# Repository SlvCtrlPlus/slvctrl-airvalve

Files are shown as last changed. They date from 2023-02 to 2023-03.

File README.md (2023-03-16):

# slvctrl-airvalve

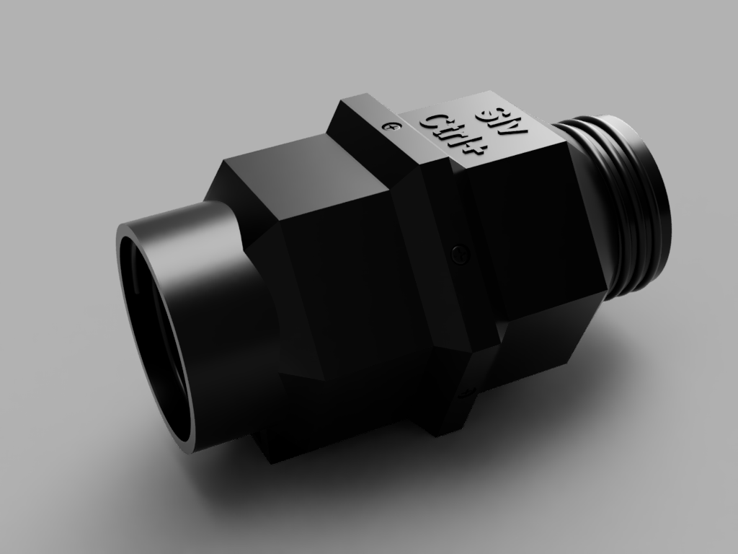
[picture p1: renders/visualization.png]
Air Valve Visualization


## Schema
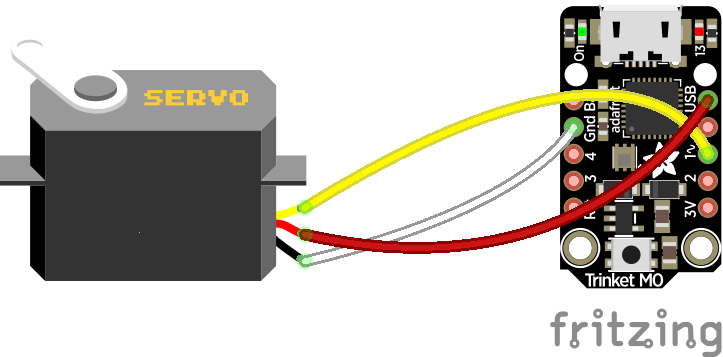
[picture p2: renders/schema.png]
Schema


## Required libraries
* https://github.com/ppedro74/Arduino-SerialCommands
* https://github.com/arduino-libraries/Servo

## Printing
The files can be found in the [stl/](./stl) folder of this repository.

### Material
Good results were achieved using ABS and PETG. PLA was not tested, but may also work out fine. 
For the ValvePlate_TPU.stl a flexible material like TPU is a must to ensure a good seal

### Perimeters
A minimum of three (3) are recommended for stability, but less can work out fine as well (your mileage may vary)

### Infill
30%  with Grid, Triangles or Cubic is recommended.

### Supports
The slvctrl-airvalve was designed to be printed with minimal need for supports. The ValveBox_Front.stl requires 
supports to bridge valve plate holder and the ValveBox_Rear.stl requires a support under the USB-Port. 
Refer to the picture for placement on the build plate.

## BOM
* 1x SG90 micro servo 9g
* 1x Adafruit Trinket M0
* 20x M2x8 self-tapping screws

## Construction
Combine the components adding screws where necessary. Consult the image for reference.
The servo cable will have to be cut and shortened, then fed through the hole in the ValveBox_RearTrinketMount.stl 
and then soldered to the trinket connections.

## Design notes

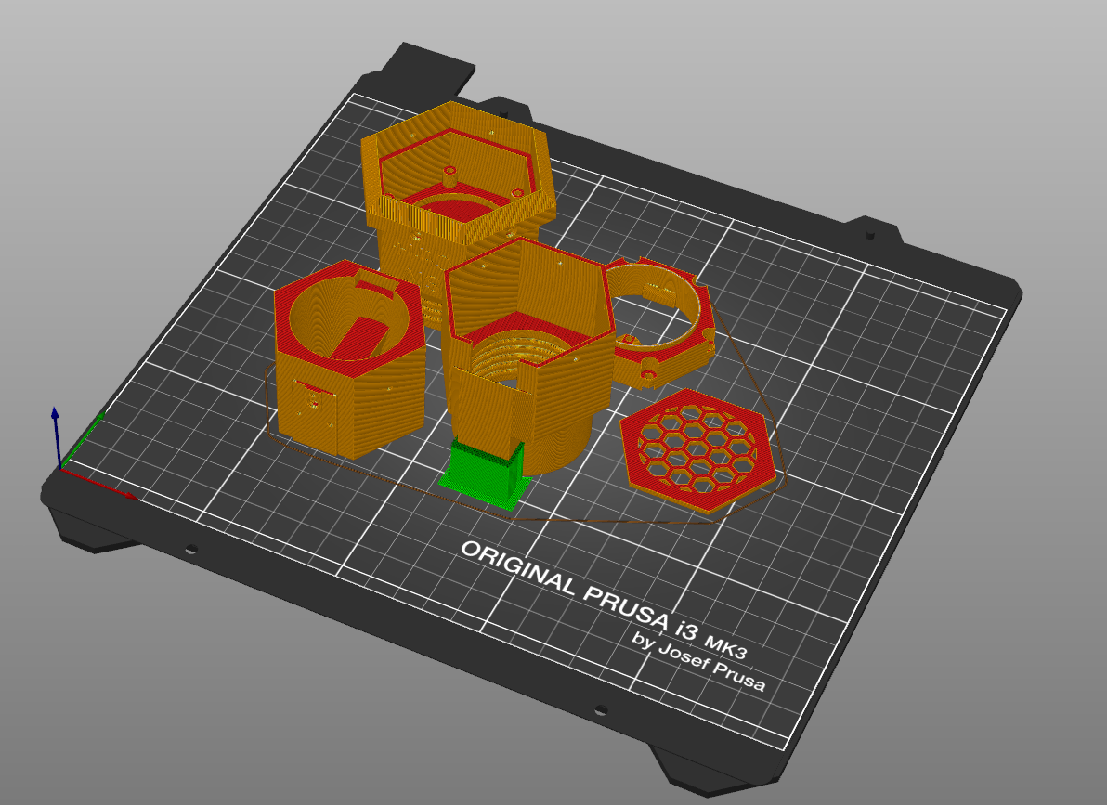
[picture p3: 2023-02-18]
renders/slicer.png

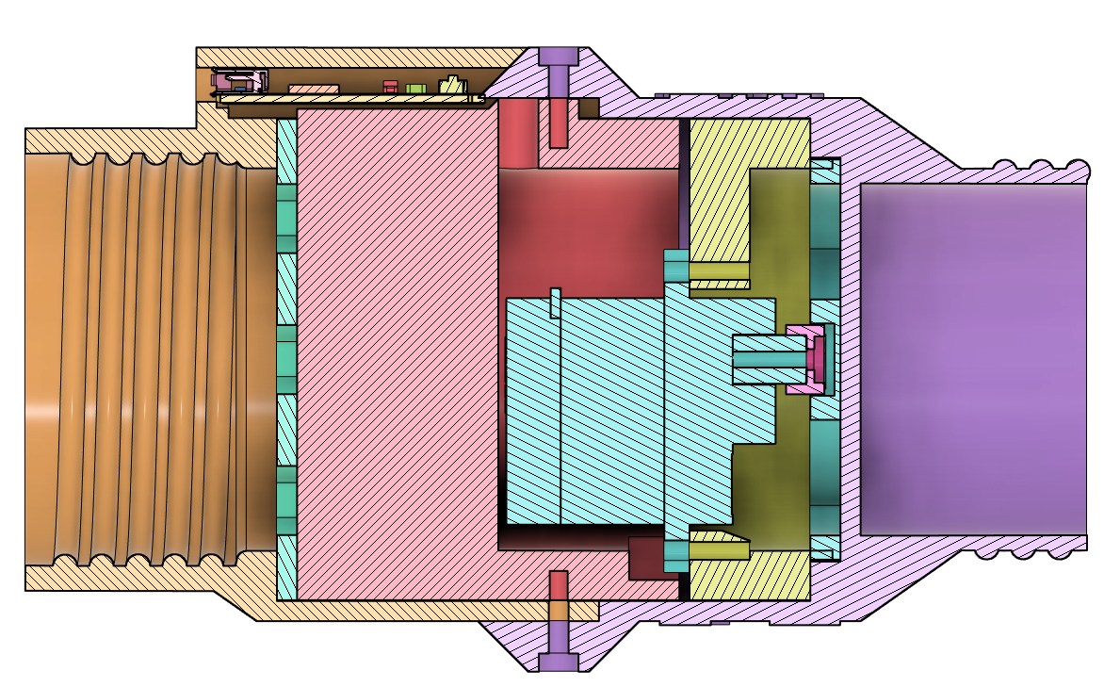
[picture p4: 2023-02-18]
renders/composition-view-02.png

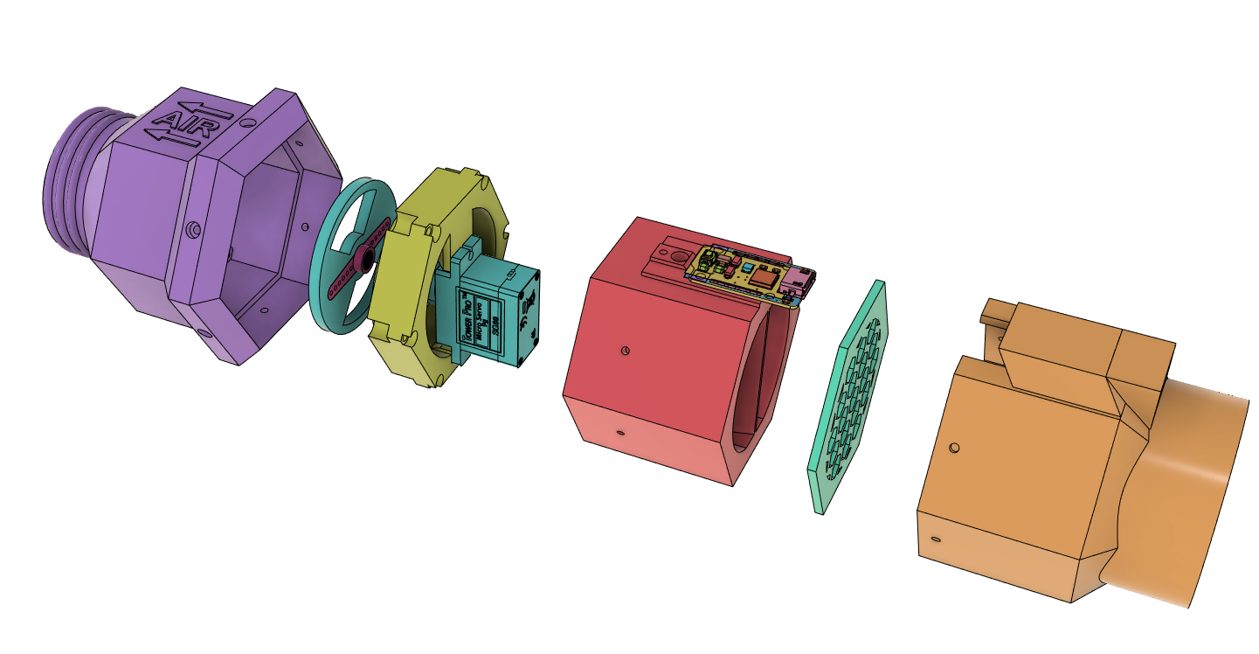
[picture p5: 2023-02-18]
renders/composition-view-01.png

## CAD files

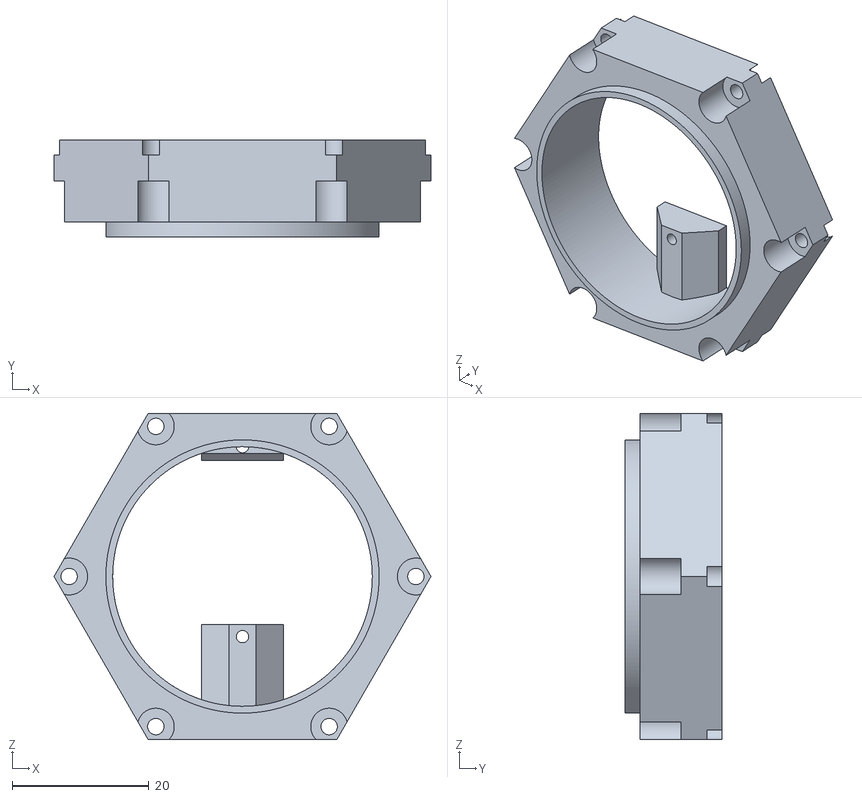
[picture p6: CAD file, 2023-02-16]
stl/ValveBox_FrontServoMount.stl
55.2 x 14.2 x 47.8

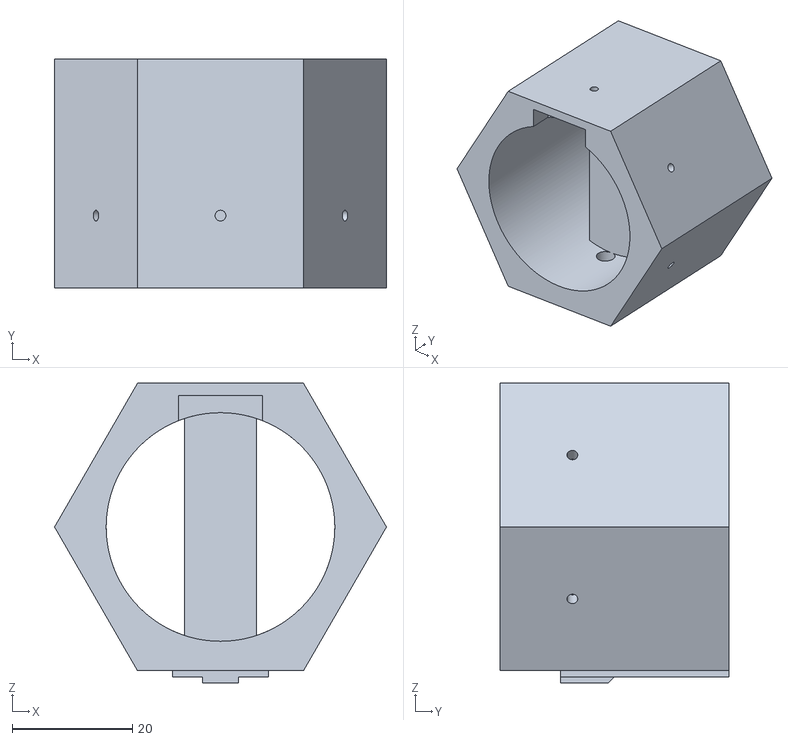
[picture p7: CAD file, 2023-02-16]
stl/ValveBox_RearTrinketMount.stl
55.2 x 38.0 x 49.8

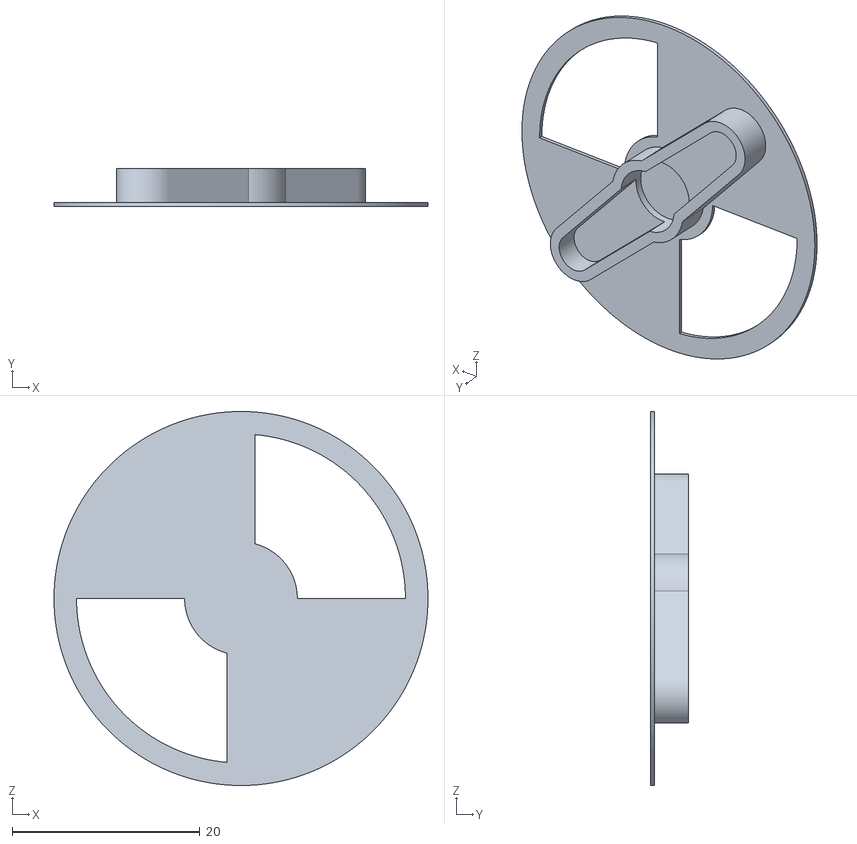
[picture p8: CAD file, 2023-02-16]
stl/ValvePlate_TPU.stl
39.8 x 4.00 x 39.8

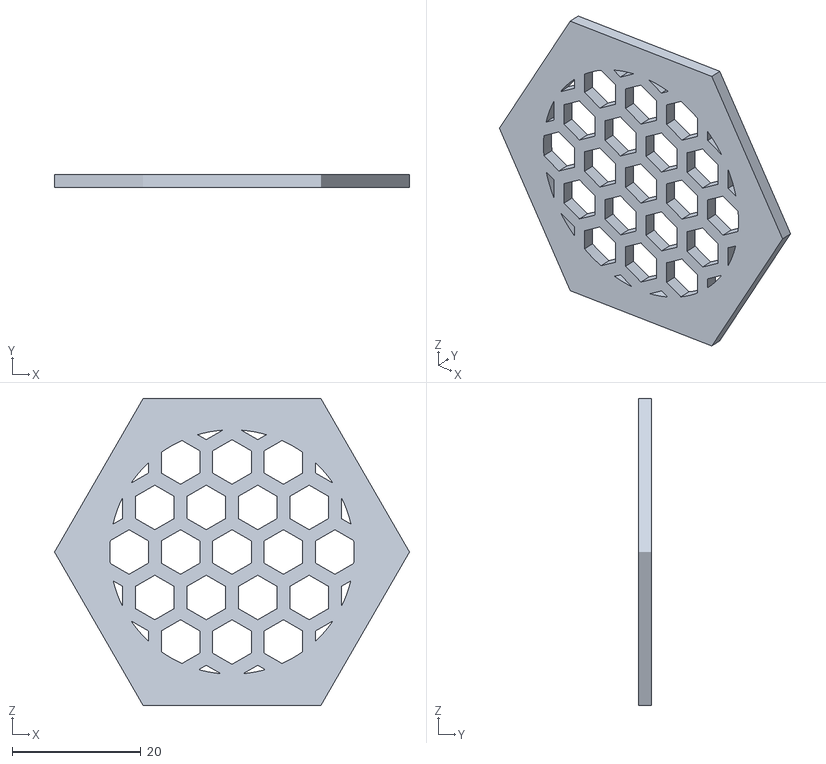
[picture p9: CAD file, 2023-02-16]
stl/ValveBox_RearGrate.stl
55.2 x 2.00 x 47.8

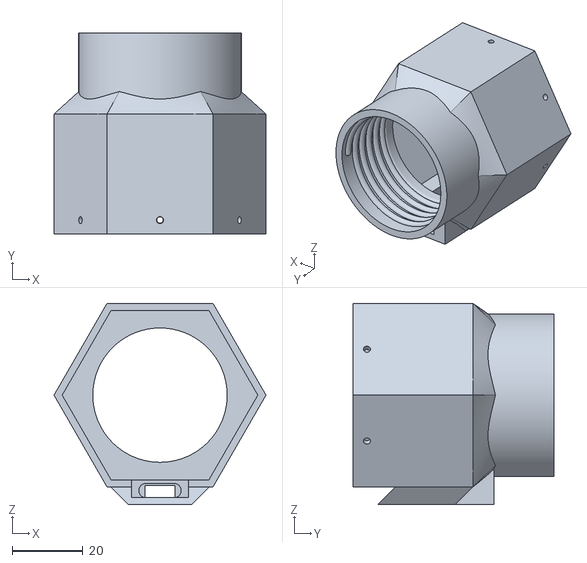
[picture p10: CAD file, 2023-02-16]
stl/ValveBox_Rear.stl
60.0 x 57.0 x 57.0

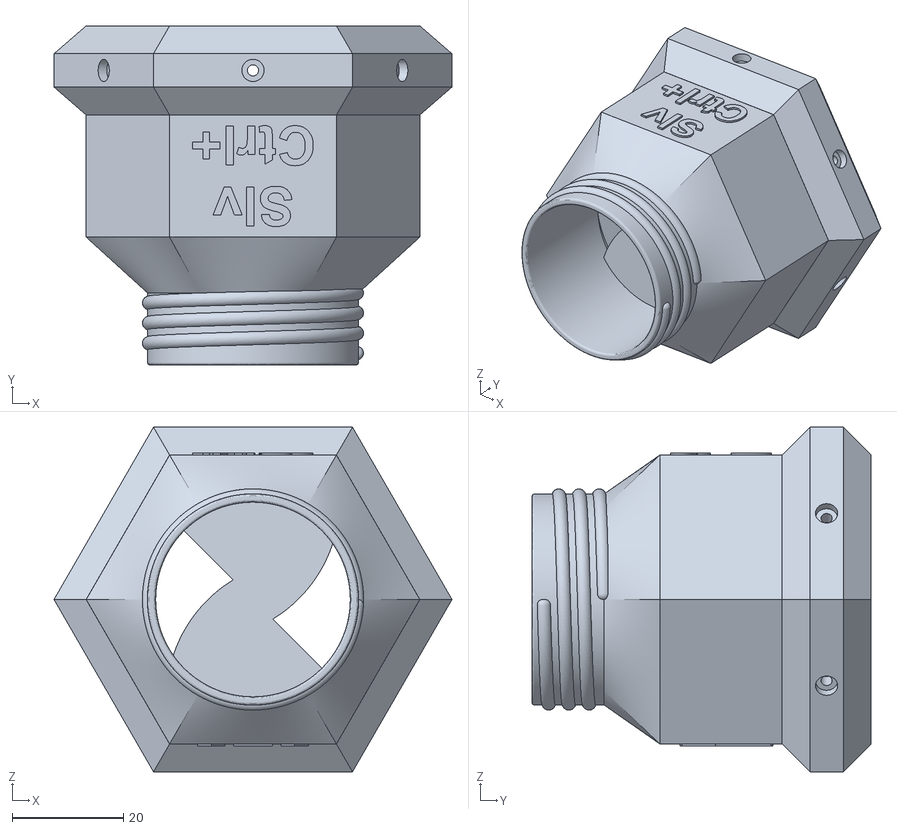
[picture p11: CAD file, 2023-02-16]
stl/ValveBox_Front.stl
71.6 x 61.0 x 62.0

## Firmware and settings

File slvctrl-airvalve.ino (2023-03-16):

#include <Servo.h>
#include <math.h>
#include <SerialCommands.h>

const char* DEVICE_TYPE = "air_valve";
const int FM_VERSION = 10000; // 1.00.00
const int PROTOCOL_VERSION = 10000; // 1.00.00

const int SERVO_PWM_PIN = 1;
const int ANGLE_OPEN = 10;
const int ANGLE_CLOSED = 85;

Servo servo;
int currentFlow = 0;

char serial_command_buffer[32];
SerialCommands serialCommands(&Serial, serial_command_buffer, sizeof(serial_command_buffer), "\n", " ");

void commandIntroduce(SerialCommands* sender);
void commandStress(SerialCommands* sender);
void commandFlowGet(SerialCommands* sender);
void commandFlowSet(SerialCommands* sender);

void setup() {
    servo.attach(SERVO_PWM_PIN);
    servo.write(ANGLE_OPEN); // set to open
    currentFlow = 100;
    
    Serial.begin(9600);

    // Add commands
    serialCommands.SetDefaultHandler(commandUnrecognized);
    serialCommands.AddCommand(new SerialCommand("introduce", commandIntroduce));
    serialCommands.AddCommand(new SerialCommand("status", commandStatus));
    serialCommands.AddCommand(new SerialCommand("attributes", commandAttributes));
    serialCommands.AddCommand(new SerialCommand("stress", commandStress));
    serialCommands.AddCommand(new SerialCommand("get-flow", commandGetFlow));
    serialCommands.AddCommand(new SerialCommand("set-flow", commandSetFlow));
    serialCommands.AddCommand(new SerialCommand("angle-get", commandAngleGet));
    serialCommands.AddCommand(new SerialCommand("angle-set", commandAngleSet));

    serialCommands.GetSerial()->write(0x07);
}

void loop() {
    serialCommands.ReadSerial();
}

void commandIntroduce(SerialCommands* sender) {
    serial_printf(sender->GetSerial(), "introduce;%s,%d,%d\n", DEVICE_TYPE, FM_VERSION, PROTOCOL_VERSION);
}

void commandStatus(SerialCommands* sender) {
    serial_printf(sender->GetSerial(), "status;flow:%d\n", currentFlow);
}

void commandAttributes(SerialCommands* sender) {
    serial_printf(sender->GetSerial(), "attributes;flow:rw[0-100]\n");
}

void commandSetFlow(SerialCommands* sender) {
    char* percentageStr = sender->Next();

    if (percentageStr == NULL) {
        sender->GetSerial()->println("set-flow;;status:failed,reason:percentage_param_missing\n");
        return;
    }
  
    int percentage = atoi(percentageStr);
  
    setFlow(percentage, 0);

    serial_printf(sender->GetSerial(), "set-flow;%d;status:successful\n", getFlow());
}

void commandGetFlow(SerialCommands* sender) {
    serial_printf(sender->GetSerial(), "get-flow;%d\n", getFlow());
}

void commandAngleGet(SerialCommands* sender) {
    serial_printf(sender->GetSerial(), "angle-get,%d\n", servo.read());
}

void commandAngleSet(SerialCommands* sender) {
    char* angleStr = sender->Next();
    int angle = atoi(angleStr);

    servo.write(angle);
    
    serial_printf(sender->GetSerial(), "angle-set,%d\n", servo.read());
}

void commandStress(SerialCommands* sender) {
  char* roundsStr = sender->Next();

  if (roundsStr == NULL) {
      sender->GetSerial()->println("Rounds parameter missing\n");
      return;
  }
  
  int rounds = atoi(roundsStr);
  
  for (int i = 0; i < rounds; i++) {
      servo.write(ANGLE_CLOSED);
      serial_printf(sender->GetSerial(), "Stress round %d: closed\n", i);
      delay(1000);

      servo.write(ANGLE_OPEN);
      serial_printf(sender->GetSerial(), "Stress round %d: opened\n", i);
      delay(1000);
  }
}

void commandUnrecognized(SerialCommands* sender, const char* cmd)
{
    serial_printf(sender->GetSerial(), "Unrecognized command [%s]\n", cmd);
}

void setFlow(int percentage, int fade) {
    int currentAngle = servo.read();
    int newAngle = ANGLE_OPEN + ((int) round((100 - percentage) * (ANGLE_CLOSED-ANGLE_OPEN) * 0.01));
    int diff = newAngle-currentAngle;

    if (newAngle == currentAngle) {
        // Same angle, don't do anything
        return;
    }

    if (fade > 0) {
        int diffAbs = abs(diff);
        int waitPerStep = round(fade/diffAbs);
        int stepDirection = (newAngle > currentAngle) ? +1 : -1;
    
        while (currentAngle != newAngle) {
            currentAngle += stepDirection;
            servo.write(currentAngle);
            delay(waitPerStep);
        }
    } else {
        servo.write(newAngle);
        currentAngle = newAngle;
    }

    currentFlow = percentage;
}

int getFlow() {
    return 100 - round((servo.read() - ANGLE_OPEN) * 100 / (ANGLE_CLOSED-ANGLE_OPEN));
}

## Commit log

2022-07-14 Fix initial flow value
    [slvctrl-airvalve.ino]
2023-02-16 Add STL files
    [ValveBox_Front.stl, ValveBox_FrontServoMount.stl, ValveBox_Rear.stl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]
2023-02-18 Add all printing information
